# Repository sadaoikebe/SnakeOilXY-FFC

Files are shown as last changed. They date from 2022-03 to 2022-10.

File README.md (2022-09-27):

# FFC mod for SnakeOil-XY 3-D printer

This is a toolhead PCB suite for SnakeOil-XY 3-D printer.
* It's a combo of a toolhead PCB and a dedicated MCU. MCU is connected to the toolhead by a ribbon cable, which makes connection simpler and also makes toolhead lighter.
* It only needs USB wire and 24V power supply connected to the MCU board.
* It has an ADXL345 accelerometer on-board.
* It has an X endstop on board, which fits SnakeOilXY toolhead dimension.
* This system is compatible only with Klipper.

block diagram

## Appearance

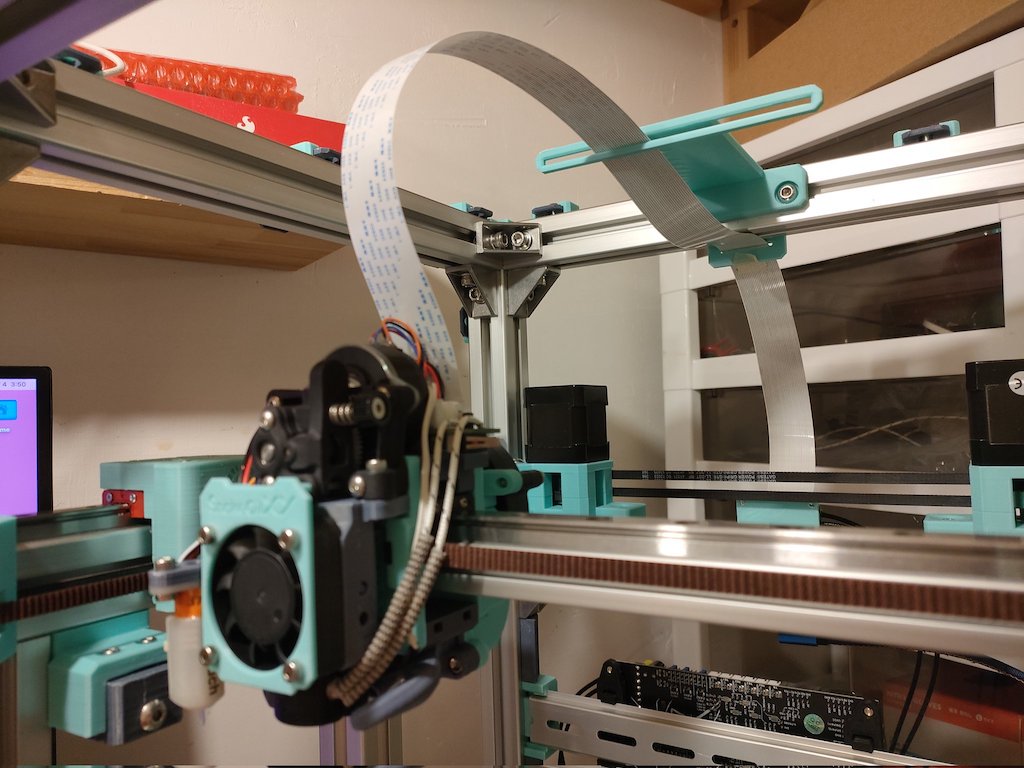
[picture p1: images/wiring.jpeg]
wiring


## Toolhead

This toolhead PCB can be attached onto adxl_mount to replace the ADXL345 PCB.

It's a toolhead PCB with an ADXL345 accelerometer on-board, and it has an X endstop which fits SnakeOil-XY toolhead dimension.

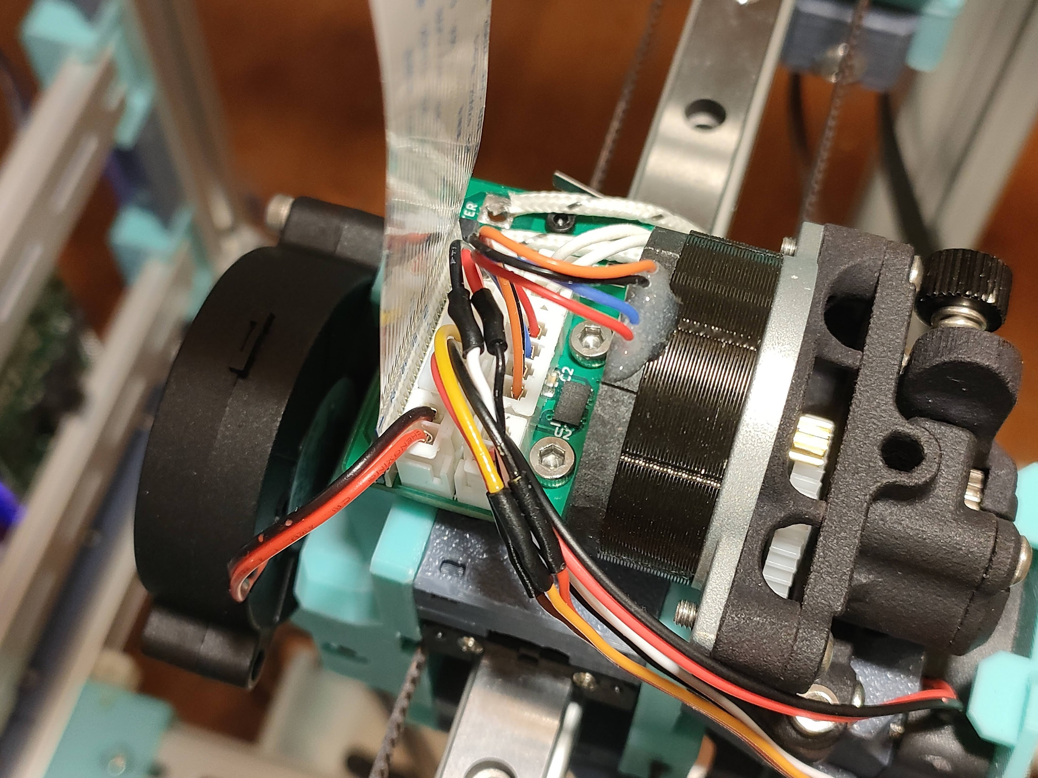
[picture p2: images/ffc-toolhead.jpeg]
Toolhead


### Toolhead board assembly

Tricky steps are:

* The two rows of the connectors are close, so two rows of connectors must be installed facing each other. Please be careful of the polarity of the hotend fan and the part cooling fan connector... (red arrow in the picture)
* Heater cables should be soldered. One of the heater terminals is close to the FFC connector, so unfortunately, screw terminal block (KF128 etc..) wouldn't fit. It's still able to disassemble without solder iron - loosening the bolt on the hotend will do the job. (yellow arrow in the picture)
* Bypass capacitor C2 is in the way of the stepper 4-pin connector. The bottom side of the stepper connector needs to be chamfered a little.
* It has Bltouch(servo) and Zmin(probe) connectors in order to use Z probes. Bltouch, inductive probe, or klicky probe can be used. See below diagram for connection.

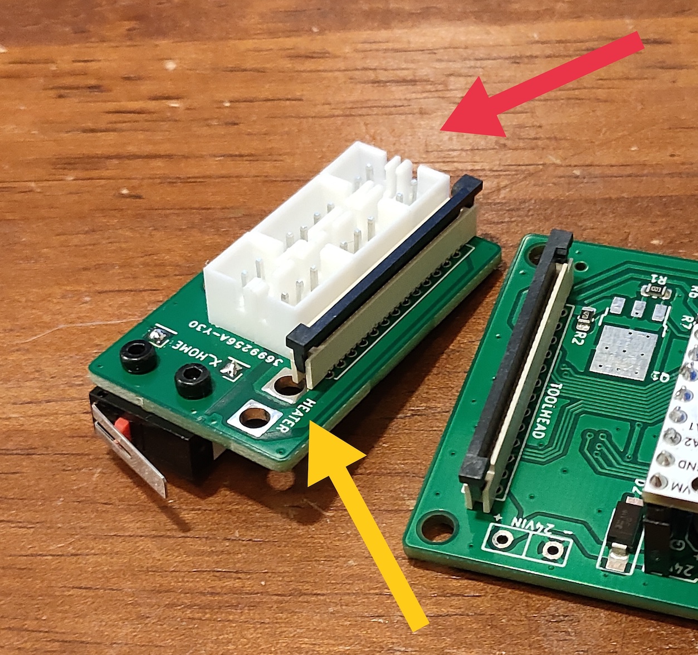
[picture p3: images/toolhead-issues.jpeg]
Toolhead


bltouch connection

induction probe connection
fan connection

### Toolhead board installation

It's designed to mount onto adxl_mount, however the X endstop switch is a bit thicker than the adxl_mount. Print and use spacer in the toolhead folder.

The back side of the stepper connector may touch the M3 bolt underneath the toolhead board. In order to avoid the unwanted contact, I recommend to cut the excess wire on the bottom and apply some capton tape to have better insulation.

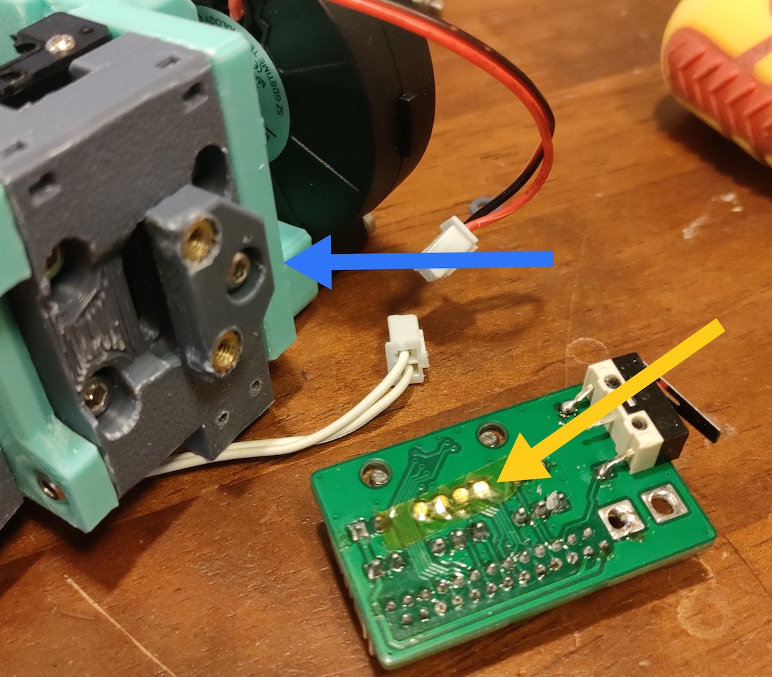
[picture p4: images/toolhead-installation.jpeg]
Toolhead


## MCU Board (revision 2)

For ease of connection, this board is dedicated to this FFC configuration. The MCU board just needs to be connected to the Raspberry Pi via USB and supplied with 24V power. A 1.0mm pitch 26-pin 20624 FFC cable is used.

It only supports UART-connected smart drivers (like TMC2209) for stepper motor driver. SPI or direct connections are not supported.

FFC connector can be soldered to either the front or back side of the board. Considering cooling and wiring, it's better to place it on the back side.

This board has schottky diode on it, so 24V probe can be connected to Zmin pin without frying the MCU.

Power => Blue LED

Heater and Fan MOSFETs => Yellow LED

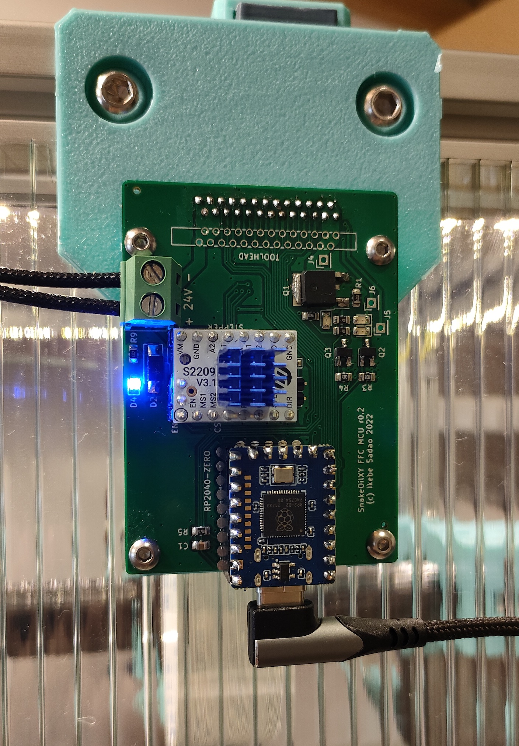
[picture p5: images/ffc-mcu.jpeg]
MCU board


### C1 capacity is too small
On the rev2 MCU board, the capacitance of C1 is 10uF, which does not stabilize the hotend temperature sensor reading enough. It would be better to add a larger capacitor in parallel or add a smooth_time setting in the [extruder] section.

## Klipper configuration

It assumes multi-mcu functionality of klipper firmware.

[sample printer.cfg](klipper/sample_printer.cfg)

## BOM

* RP2040-Zero
* 26-pin 350mm (180 model) / 450mm (250 model) 20624 FFC cable
* 2x 26-pin vertical thru-hole FFC receptacle
* 2x WSF3085 (MOSFET Heater)
* 2x PL4009 (MOSFET Fan)
* Stepper driver TMC2209 or other (UART connected "smart" drivers are must)
* 2-pin DC Terminal (KF128) for 24V power supply
* TVS diode (SMAJ28A) , schottky diode (1N5819) 40V
* 2x 8-pin socket (for stepper driver)
* Jumper pins
* Capacitors, resistors
* XH2.54 sockets (3x 2pin, 2x 3pin, 1x 4pin)

## TODO

### r0.1 --> r0.2

* The Drain and Source connections of the MOSFETs of the heater were reversed --> I changed the connections.
* TVS diode are reversed --> Thankfully JLCPCB engineer fixed it. Need to rotate next time.
* The clearance between the power supply/heater terminals and other parts are not enough --> Need increase the clearance.

### r0.2 --> r0.3

* Change MCU to genuine Pico as RP2040-Zero appears to be a bit unreliable
* add wiring and pattern for MAX31865 and PT100 thermistor
* add KF301 terminal for heater
* add AUX line
* add medusa toolhead support - allow for various X endstop placement

## Heater connection

The heater is assumed to be a 24V 50W, using 4 FFC cable contacts in parallel. Approx. 500mA current flows per contact.
Resistance of the heater wire is 266mΩ round trip including four screw terminals of 24V power supply and a 600mm FFC cable - which is measured by four-terminal-pair method.
When a 24V 50W heater is used, there is a loss of about 1W including circuits, cable and contacts. (225mΩ for 53cm of lead wire, 157mΩ for 14cm of lead wire, so the loss in the circuit and FFC is 133mΩ. 266mΩ round trip. This resistance value includes the resistance of four contacts on the fixture)

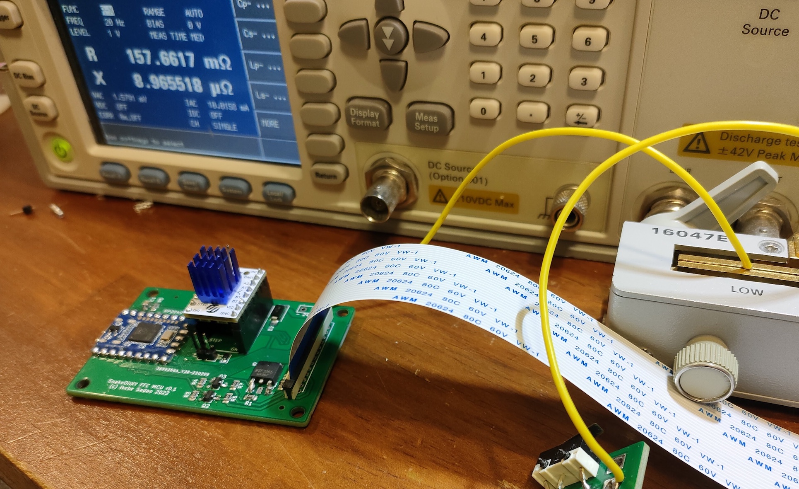
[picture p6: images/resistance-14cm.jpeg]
resistance-14cm

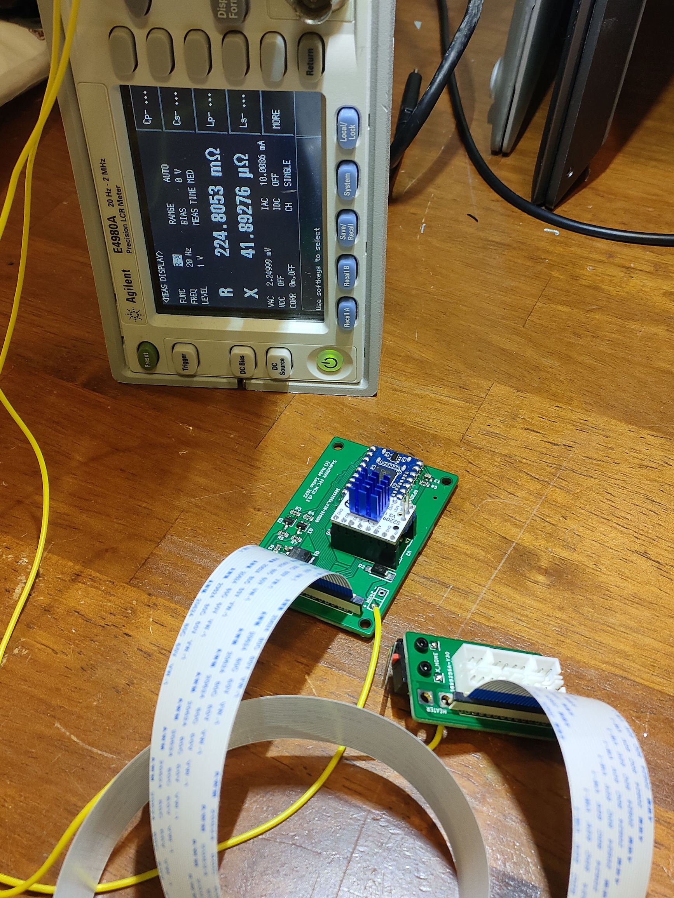
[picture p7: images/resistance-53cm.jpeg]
resistance-53cm


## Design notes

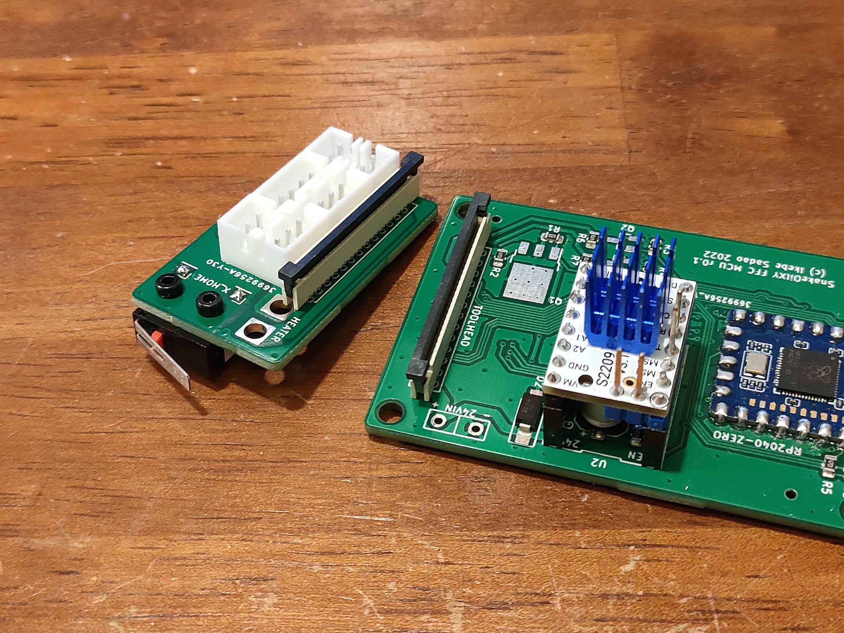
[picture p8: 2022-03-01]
images/boards.jpeg

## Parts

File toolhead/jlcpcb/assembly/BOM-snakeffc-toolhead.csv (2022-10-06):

Comment | Designator | Footprint | LCSC
0.1u | C2 | C_0603_1608Metric | C14663
ADXL345 | U2 | LGA-14_3x5mm_P0.8mm_LayoutBorder1x6y | C9667
SERVO | J11 | PinHeader_1x03_P2.54mm_Vertical
Conn_01x30 | J4 | ffc-30pin
ZMIN | J10 | PinHeader_1x03_P2.54mm_Vertical
HOTEND_FAN | J8 | PinHeader_1x02_P2.54mm_Vertical
HEATER | J5 | KF301-5.0
PARTCOOLER_FAN | J9 | PinHeader_1x02_P2.54mm_Vertical
E_STEPPER | J12 | PinHeader_1x04_P2.54mm_Vertical
X_HOME | J13 | limit_switch
AUX1 | J16 | PinHeader_1x01_P2.54mm_Vertical
PT100_NTC | J1 | PinHeader_1x04_P2.54mm_Vertical

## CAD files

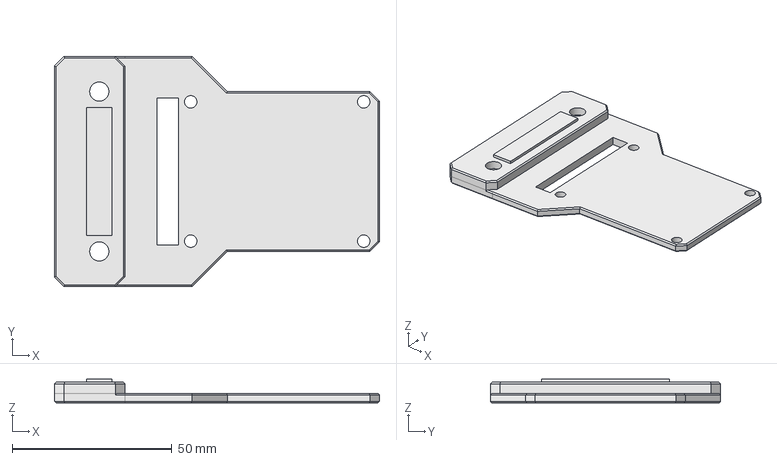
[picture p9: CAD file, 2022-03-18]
mcu2/mounter/mounter2.FCStd
101.6 x 72.0 x 7.50 mm

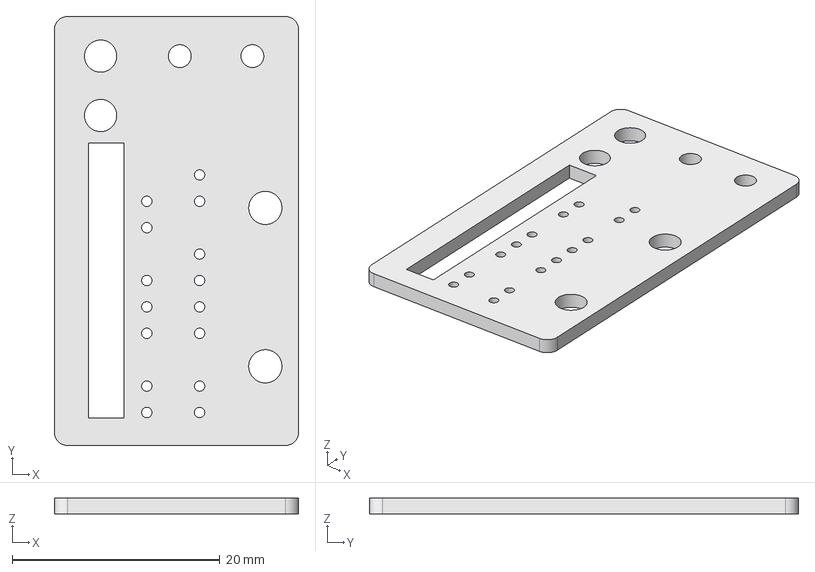
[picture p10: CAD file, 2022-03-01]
mockup/mockup.FCStd
23.5 x 41.3 x 1.50 mm

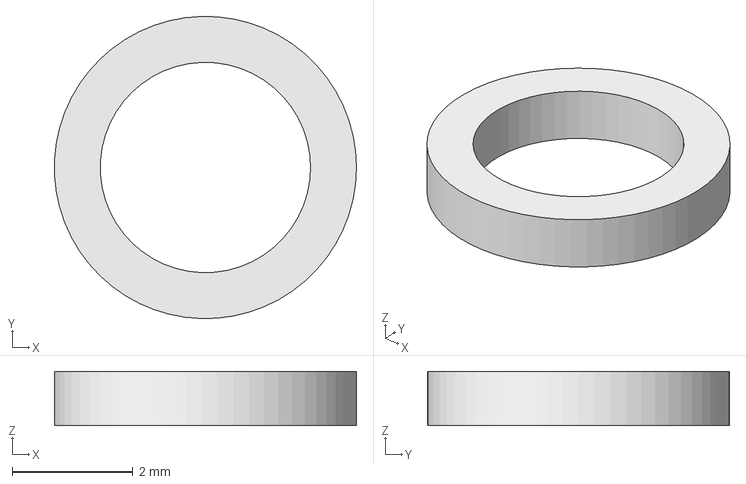
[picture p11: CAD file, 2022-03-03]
toolhead/adxl_mount_spacer.FCStd
5.00 x 5.00 x 0.9 mm

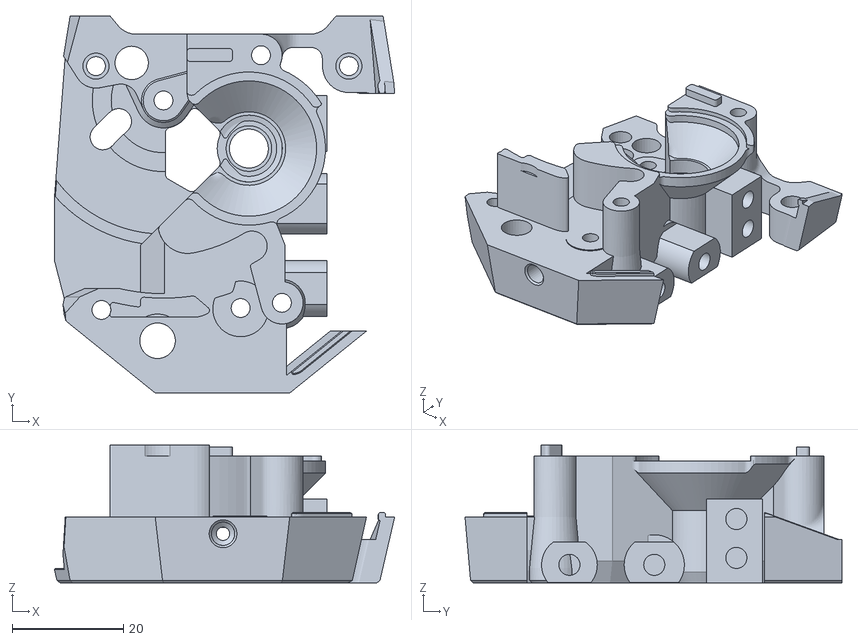
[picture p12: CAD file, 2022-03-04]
voron-clockwork2/sb-mod.stl
61.1 x 67.7 x 24.7

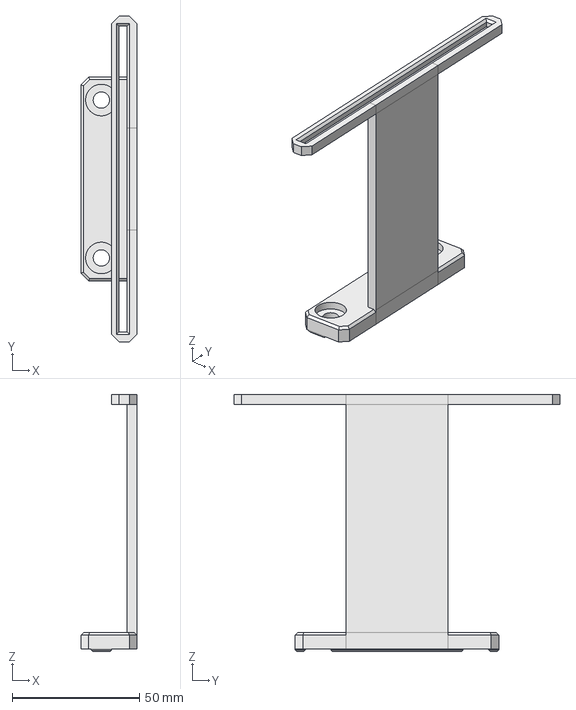
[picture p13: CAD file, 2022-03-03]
mcu2/mounter/cable-support2.FCStd
22.0 x 128.0 x 101.0 mm

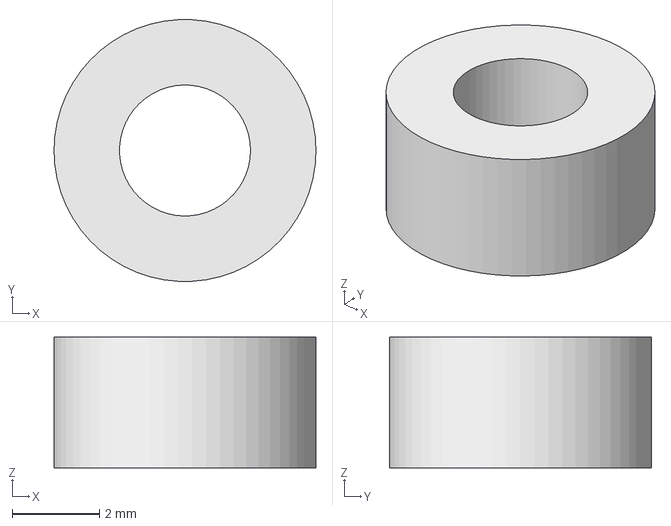
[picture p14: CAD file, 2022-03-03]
mcu2/mounter/mounter-spacer.FCStd
6.00 x 5.99 x 3.00 mm

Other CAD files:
mcu2/mounter/cable-support2.stl
mcu2/mounter/mounter-spacer.stl
mcu2/mounter/mounter2.stl
toolhead/adxl_mount_spacer.stl

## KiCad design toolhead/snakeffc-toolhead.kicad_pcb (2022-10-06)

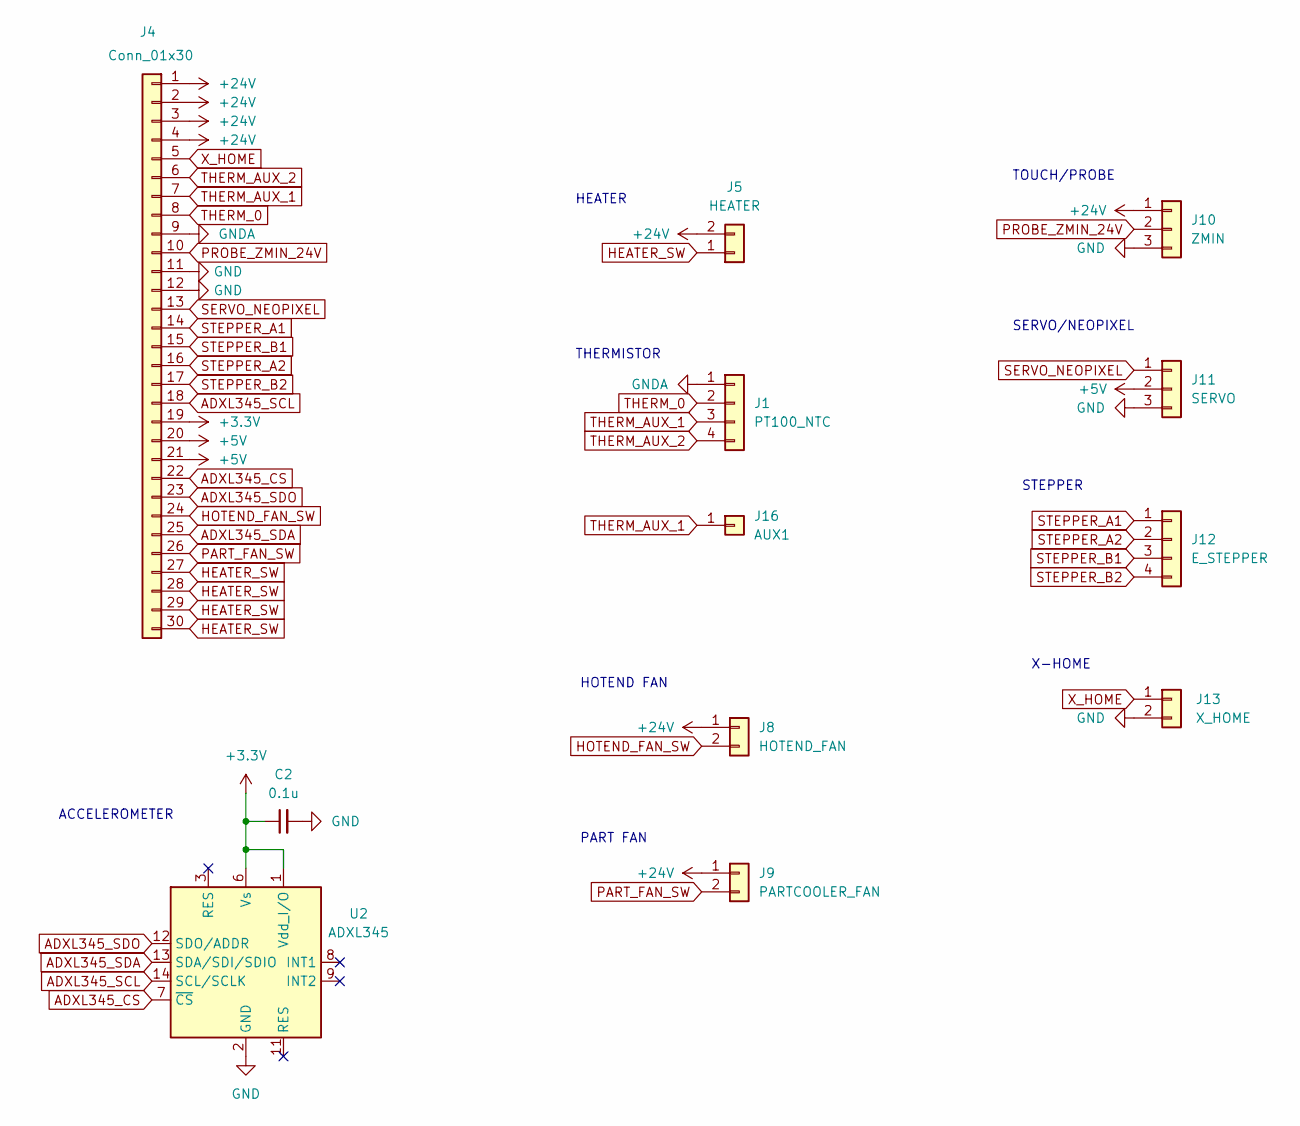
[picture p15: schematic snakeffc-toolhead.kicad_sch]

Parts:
C2: 0.1u; C_0603_1608Metric
J1: PT100_NTC; PinHeader_1x04_P2.54mm_Vertical
J4: Conn_01x30; ffc-30pin
J5: HEATER; KF301-5.0
J8: HOTEND_FAN; PinHeader_1x02_P2.54mm_Vertical
J9: PARTCOOLER_FAN; PinHeader_1x02_P2.54mm_Vertical
J10: ZMIN; PinHeader_1x03_P2.54mm_Vertical
J11: SERVO; PinHeader_1x03_P2.54mm_Vertical
J12: E_STEPPER; PinHeader_1x04_P2.54mm_Vertical
J13: X_HOME; limit_switch
J16: AUX1; PinHeader_1x01_P2.54mm_Vertical
U2: ADXL345; LGA-14_3x5mm_P0.8mm_LayoutBorder1x6y; LCSC C9667

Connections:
+3V3: C2.1, J4.19, U2.1 (Vdd_I/O), U2.6 (Vs)
+5V: J4.20, J4.21, J11.2
+24V: J4.1, J4.2, J4.3, J4.4, J5.2, J8.1, J9.1, J10.1
ADXL345_CS: J4.22, U2.7 (~CS)
ADXL345_SCL: J4.18, U2.14 (SCL/SCLK)
ADXL345_SDA: J4.25, U2.13 (SDA/SDI/SDIO)
ADXL345_SDO: J4.23, U2.12 (SDO/ADDR)
GND: C2.2, J4.11, J4.12, J10.3, J11.3, J13.2, U2.2 (GND), U2.4 (GND), U2.5 (GND)
GNDA: J1.1, J4.9
HEATER_SW: J4.27, J4.28, J4.29, J4.30, J5.1
HOTEND_FAN_SW: J4.24, J8.2
PART_FAN_SW: J4.26, J9.2
PROBE_ZMIN_24V: J4.10, J10.2
SERVO_NEOPIXEL: J4.13, J11.1
STEPPER_A1: J4.14, J12.1
STEPPER_A2: J4.16, J12.2
STEPPER_B1: J4.15, J12.3
STEPPER_B2: J4.17, J12.4
THERM_0: J1.2, J4.8
THERM_AUX_1: J1.3, J4.7, J16.1
THERM_AUX_2: J1.4, J4.6
X_HOME: J4.5, J13.1

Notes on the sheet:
PART FAN
HOTEND FAN
HEATER
STEPPER
X-HOME
ACCELEROMETER
THERMISTOR
SERVO/NEOPIXEL
TOUCH/PROBE

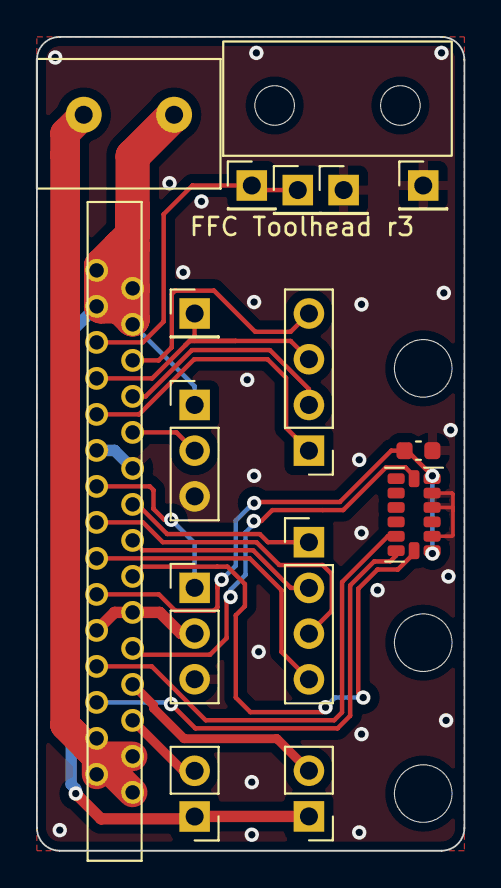
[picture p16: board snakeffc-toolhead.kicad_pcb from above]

Board: 2 copper layers, 23.7 x 45.2 mm, 12 parts (0 on the bottom side), 22 nets.

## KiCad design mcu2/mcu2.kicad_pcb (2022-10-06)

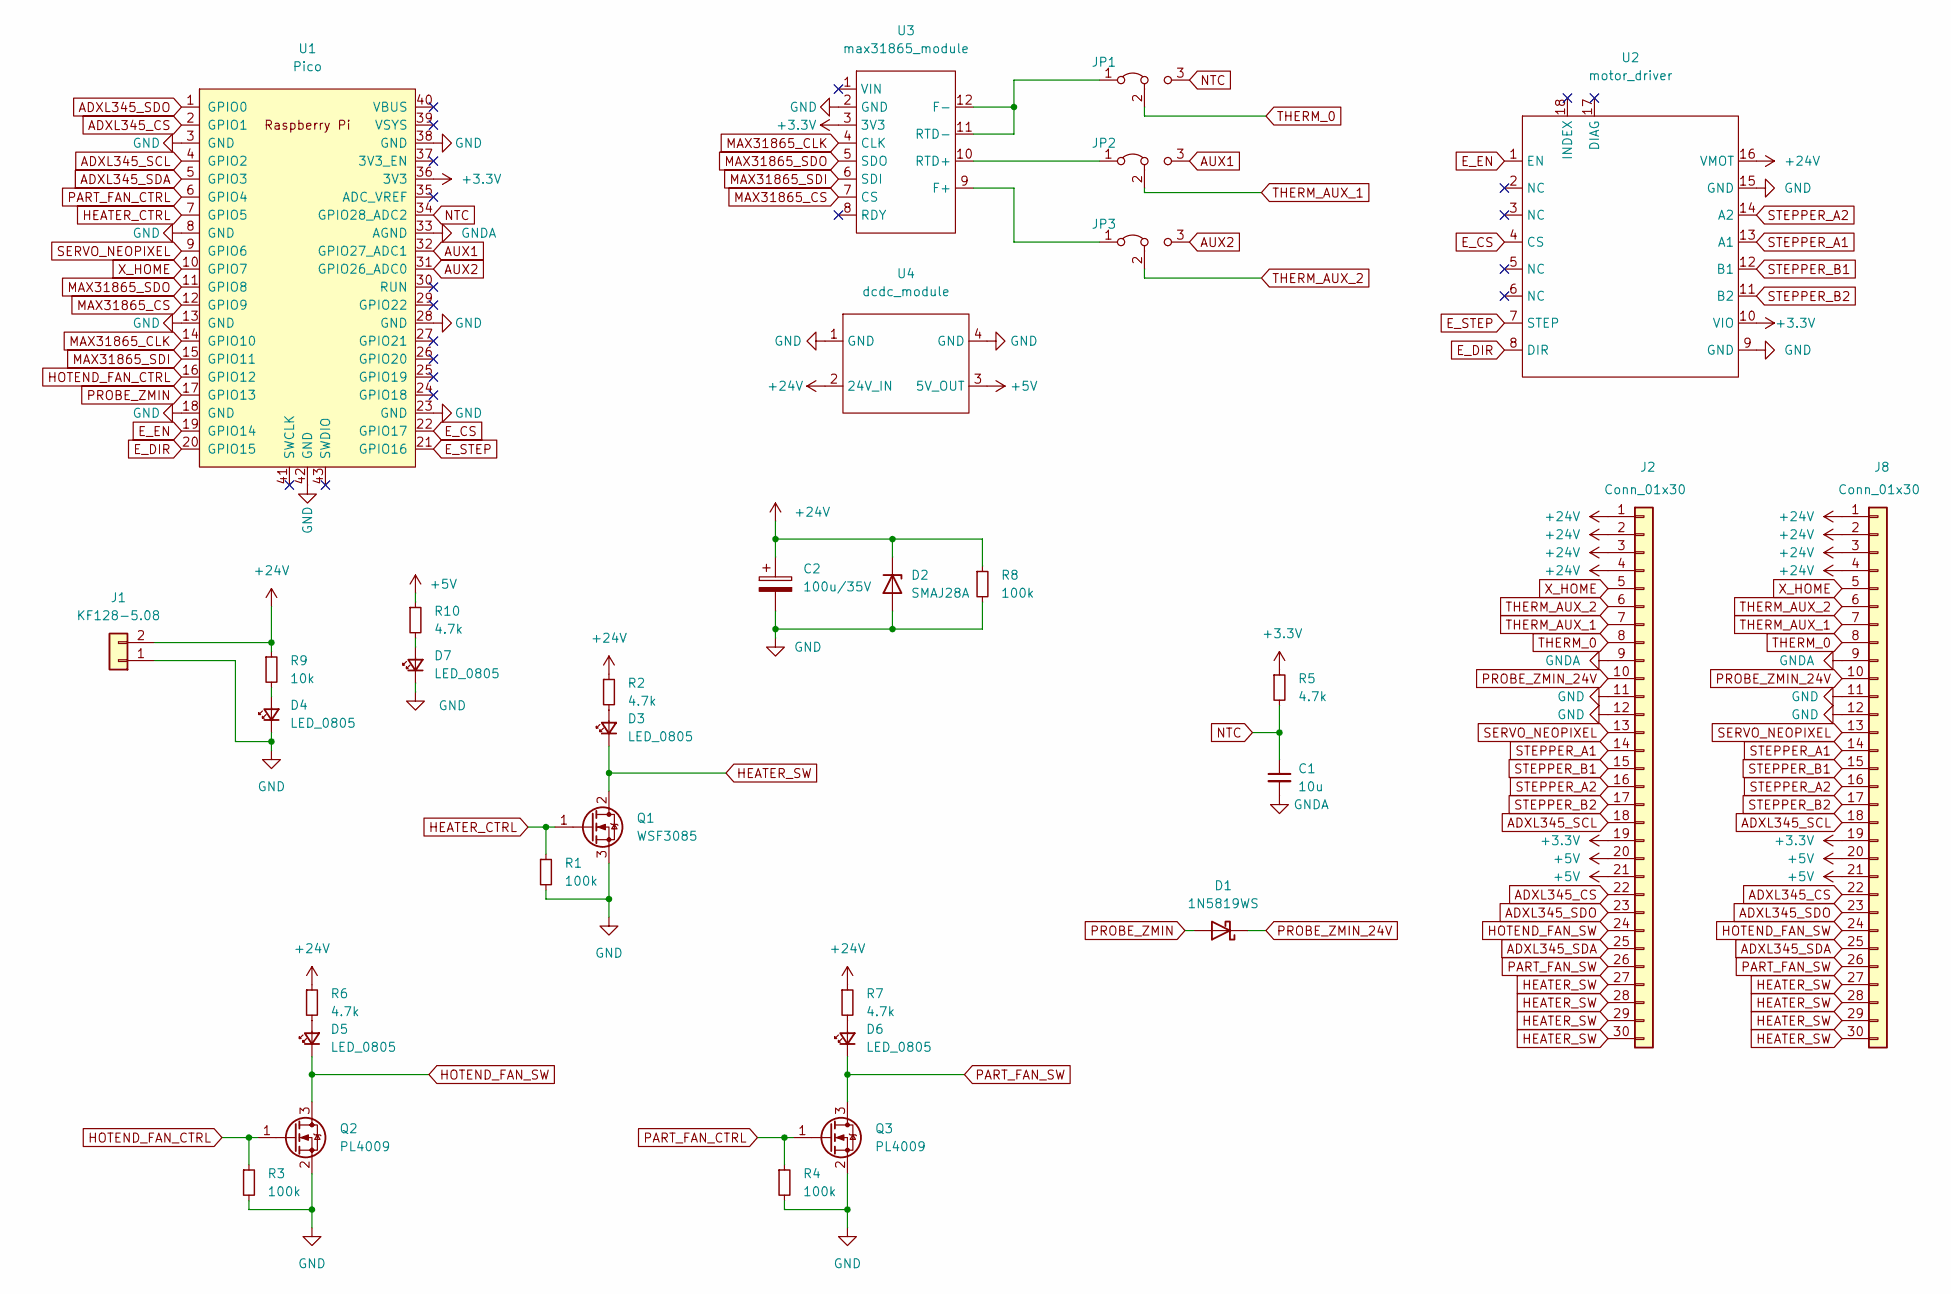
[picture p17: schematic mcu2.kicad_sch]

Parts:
C1: 10u; C_0805_2012Metric_Pad1.18x1.45mm_HandSolder
C2: 100u/35V; CP_Elec_6.3x7.7
D1: 1N5819WS; D_SOD-323_HandSoldering
D2: SMAJ28A; D_SMA_Handsoldering
D3, D4, D5, D6, D7: LED_0805; LED_0805_2012Metric_Pad1.15x1.40mm_HandSolder
J1: KF128-5.08
J2, J8: Conn_01x30; ffc-30pin
JP1, JP2, JP3: Jumper_3_Bridged12; SolderJumper-3_P1.3mm_Bridged12_RoundedPad1.0x1.5mm
Q1: WSF3085; TO-252-2
Q2, Q3: PL4009; SOT-23_Handsoldering
R1, R3, R4, R8: 100k; R_0805_2012Metric_Pad1.20x1.40mm_HandSolder
R2, R5, R6, R7, R10: 4.7k; R_0805_2012Metric_Pad1.20x1.40mm_HandSolder
R9: 10k; R_0805_2012Metric_Pad1.20x1.40mm_HandSolder
U1: Pico; RPi_Pico_SMD_TH
U2: motor_driver
U3: max31865_module; adafruit_max31865_module
U4: dcdc_module; dcdc_24v_5v_module

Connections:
+3V3: J2.19, J8.19, R5.1, U1.36 (3V3), U2.10 (VIO), U3.3 (3V3)
+5V: J2.20, J2.21, J8.20, J8.21, R10.1, U4.3 (5V_OUT)
+24V: C2.1, D2.1 (K), J1.2, J2.1, J2.2, J2.3, J2.4, J8.1, J8.2, J8.3, J8.4, R2.1, R6.1, R7.1, R8.1, R9.1, U2.16 (VMOT), U4.2 (24V_IN)
ADXL345_CS: J2.22, J8.22, U1.2 (GPIO1)
ADXL345_SCL: J2.18, J8.18, U1.4 (GPIO2)
ADXL345_SDA: J2.25, J8.25, U1.5 (GPIO3)
ADXL345_SDO: J2.23, J8.23, U1.1 (GPIO0)
AUX1: JP2.3 (B), U1.32 (GPIO27_ADC1)
AUX2: JP3.3 (B), U1.31 (GPIO26_ADC0)
E_CS: U1.22 (GPIO17), U2.4 (CS)
E_DIR: U1.20 (GPIO15), U2.8 (DIR)
E_EN: U1.19 (GPIO14), U2.1 (EN)
E_STEP: U1.21 (GPIO16), U2.7 (STEP)
GND: C2.2, D2.2 (A), D4.1 (K), D7.1 (K), J1.1, J2.11, J2.12, J8.11, J8.12, Q1.3 (S), Q2.2 (S), Q3.2 (S), R1.2, R3.2, R4.2, R8.2, U1.3 (GND), U1.8 (GND), U1.13 (GND), U1.18 (GND), U1.23 (GND), U1.28 (GND), U1.38 (GND), U1.42 (GND), U2.9 (GND), U2.15 (GND), U3.2 (GND), U4.1 (GND), U4.4 (GND)
GNDA: C1.2, J2.9, J8.9, U1.33 (AGND)
HEATER_CTRL: Q1.1 (G), R1.1, U1.7 (GPIO5)
HEATER_SW: D3.1 (K), J2.27, J2.28, J2.29, J2.30, J8.27, J8.28, J8.29, J8.30, Q1.2 (D)
HOTEND_FAN_CTRL: Q2.1 (G), R3.1, U1.16 (GPIO12)
HOTEND_FAN_SW: D5.1 (K), J2.24, J8.24, Q2.3 (D)
MAX31865_CLK: U1.14 (GPIO10), U3.4 (CLK)
MAX31865_CS: U1.12 (GPIO9), U3.7 (CS)
MAX31865_SDI: U1.15 (GPIO11), U3.6 (SDI)
MAX31865_SDO: U1.11 (GPIO8), U3.5 (SDO)
NTC: C1.1, JP1.3 (B), R5.2, U1.34 (GPIO28_ADC2)
unnamed: D3.2 (A), R2.2
unnamed: D4.2 (A), R9.2
unnamed: D5.2 (A), R6.2
unnamed: D6.2 (A), R7.2
unnamed: D7.2 (A), R10.2
unnamed: JP1.1 (A), U3.11 (RTD-), U3.12 (F-)
unnamed: JP2.1 (A), U3.10 (RTD+)
unnamed: JP3.1 (A), U3.9 (F+)
PART_FAN_CTRL: Q3.1 (G), R4.1, U1.6 (GPIO4)
PART_FAN_SW: D6.1 (K), J2.26, J8.26, Q3.3 (D)
PROBE_ZMIN: D1.2 (A), U1.17 (GPIO13)
PROBE_ZMIN_24V: D1.1 (K), J2.10, J8.10
SERVO_NEOPIXEL: J2.13, J8.13, U1.9 (GPIO6)
STEPPER_A1: J2.14, J8.14, U2.13 (A1)
STEPPER_A2: J2.16, J8.16, U2.14 (A2)
STEPPER_B1: J2.15, J8.15, U2.12 (B1)
STEPPER_B2: J2.17, J8.17, U2.11 (B2)
THERM_0: J2.8, J8.8, JP1.2 (C)
THERM_AUX_1: J2.7, J8.7, JP2.2 (C)
THERM_AUX_2: J2.6, J8.6, JP3.2 (C)
X_HOME: J2.5, J8.5, U1.10 (GPIO7)

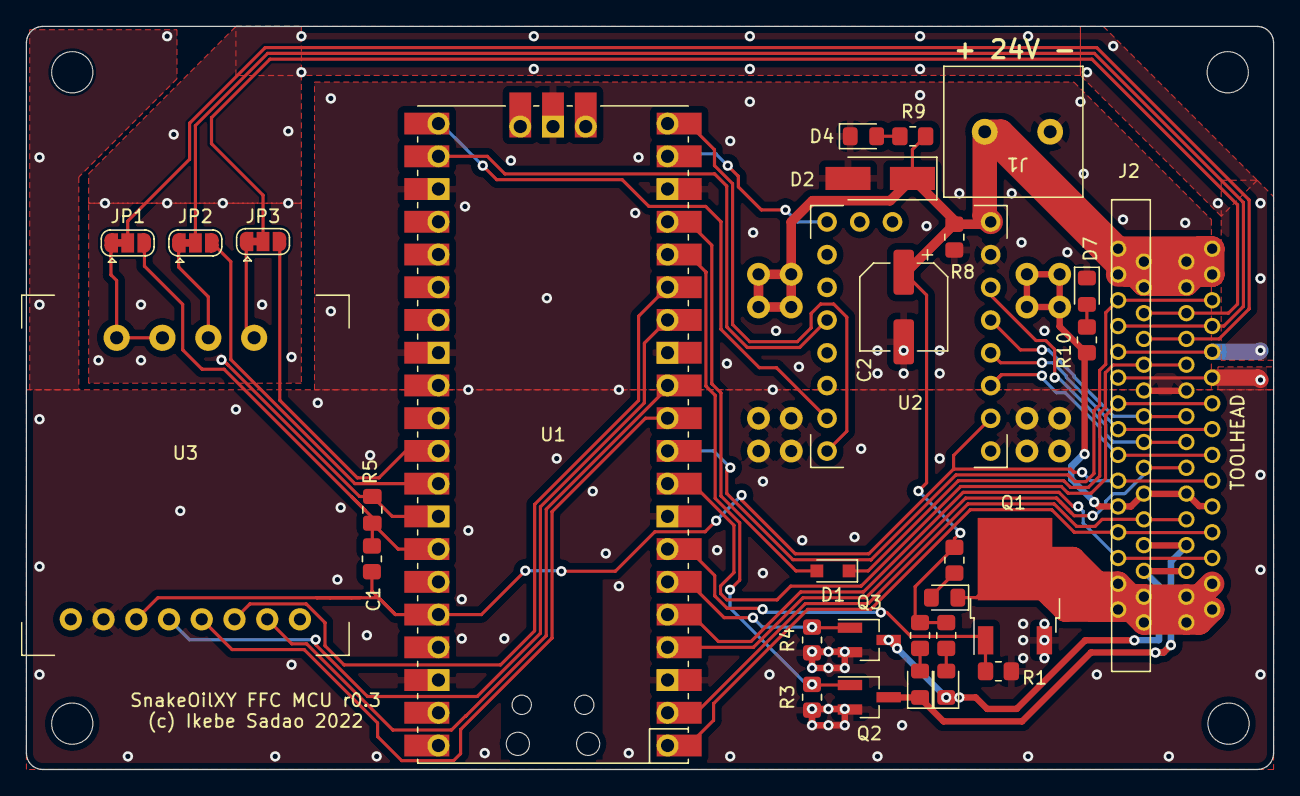
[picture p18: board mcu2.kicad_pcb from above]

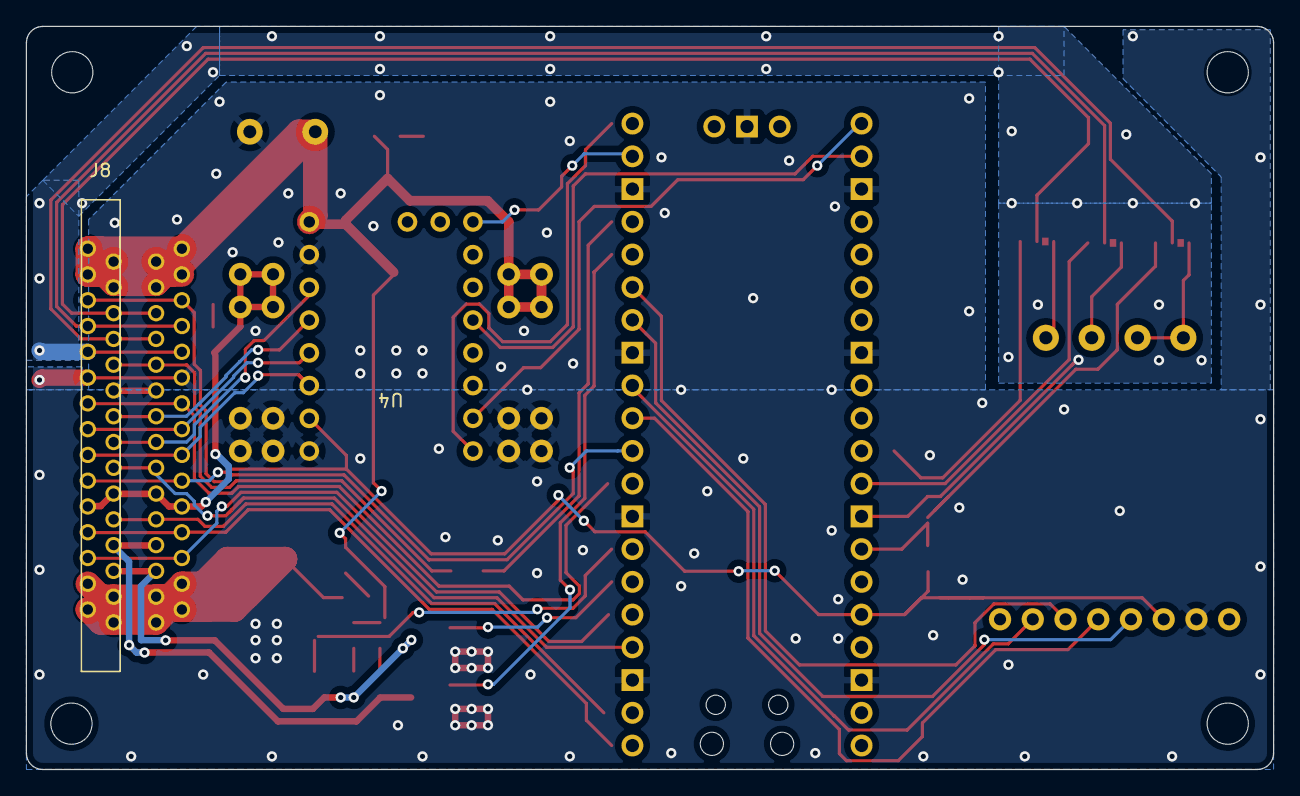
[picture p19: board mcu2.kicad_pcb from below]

Board: 2 copper layers, 96.8 x 57.7 mm, 32 parts (2 on the bottom side), 45 nets.

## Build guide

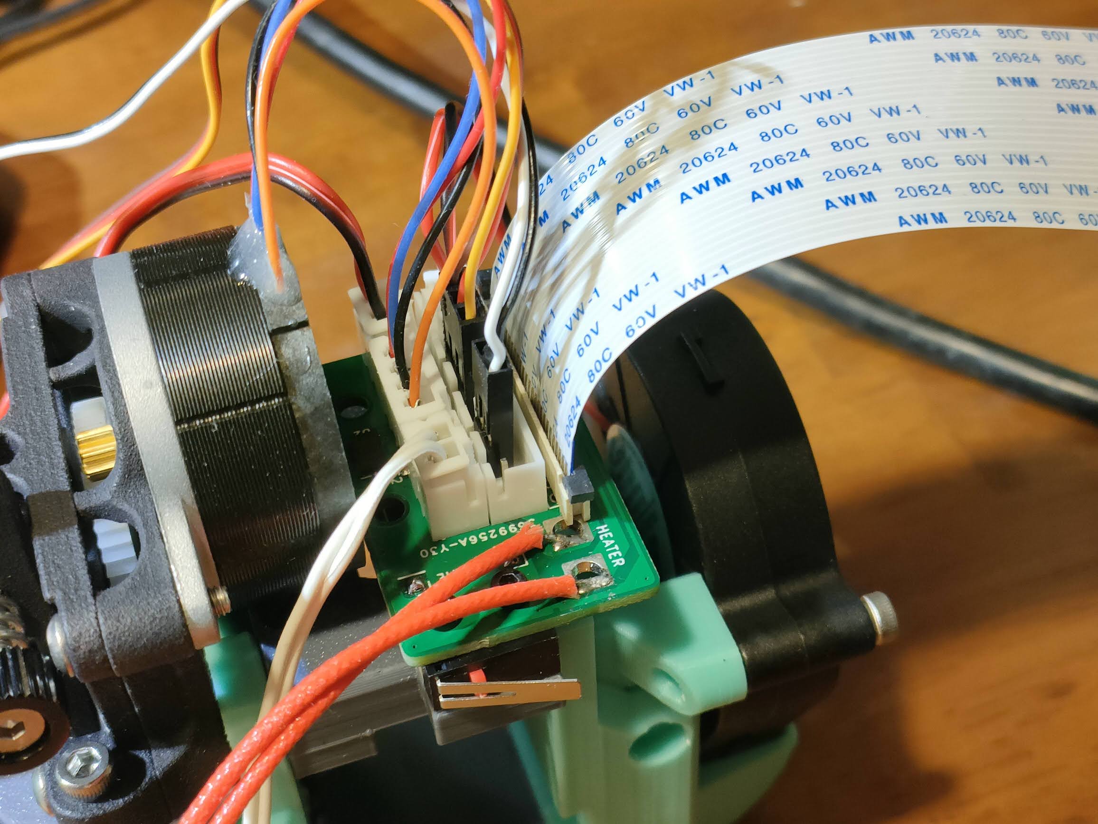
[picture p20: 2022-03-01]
images/toolhead-installed.jpeg

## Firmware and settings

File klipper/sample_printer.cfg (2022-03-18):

[include kiauh_macros.cfg]
[mcu]
serial: /dev/serial/by-id/usb-Klipper_stm32f446xx_160021001850563046363120-if00

[mcu toolhead]
serial: /dev/serial/by-id/usb-Klipper_rp2040_E66138935F119829-if00

[printer]
kinematics: corexy
max_velocity: 300  
max_accel: 10000
max_z_velocity: 15
max_z_accel: 350
square_corner_velocity: 5.0

[stepper_x]
step_pin: PE11
dir_pin: !PE10
enable_pin: !PE9
rotation_distance: 40
microsteps: 16
full_steps_per_rotation:400
endstop_pin: ^toolhead:gpio8
position_min: 0

position_endstop: 180
position_max: 180

homing_speed: 100
homing_retract_dist: 5
homing_positive_dir: true

[tmc2209 stepper_x]
uart_pin: PE7
interpolate: True
run_current: 0.7
hold_current: 0.4
sense_resistor: 0.110
stealthchop_threshold: 0

[stepper_y]
step_pin: PD8
dir_pin: !PB12
enable_pin: !PD9
rotation_distance: 40
microsteps: 16
full_steps_per_rotation:400
endstop_pin: ^PB13
position_min: 0

position_endstop: 180
position_max: 180

homing_speed: 100
homing_retract_dist: 5
homing_positive_dir: true

[tmc2209 stepper_y]
uart_pin: PE15
interpolate: True
run_current: 0.7
hold_current: 0.4
sense_resistor: 0.110
stealthchop_threshold: 0

[stepper_z]
step_pin: PD14
dir_pin: !PD13
enable_pin: !PD15
rotation_distance: 40
gear_ratio: 80:16
microsteps: 16
#endstop_pin: ^PA0
#position_endstop: 0
endstop_pin: probe:z_virtual_endstop
position_max: 180

position_min: -5
homing_speed: 8
second_homing_speed: 3
homing_retract_dist: 3

[safe_z_home]
home_xy_position: 90, 90
speed: 100
z_hop: 10
z_hop_speed: 5

[tmc2209 stepper_z]
uart_pin: PD10
uart_address: 0
interpolate: True
run_current: 0.7
hold_current: 0.4
sense_resistor: 0.110
stealthchop_threshold: 0

[adxl345]
cs_pin: toolhead:gpio1
spi_bus: spi0a

[resonance_tester]
accel_chip: adxl345
probe_points: 90, 90, 20

[bltouch]
sensor_pin: ^toolhead:gpio9
control_pin: toolhead:gpio7
z_offset: 0

[pause_resume]

[display_status]

[virtual_sdcard]
path: ~/gcode_files

##	In E0-MOT Position
[extruder]
step_pin: toolhead:gpio12
dir_pin: toolhead:gpio11
enable_pin: !toolhead:gpio10

rotation_distance: 22.6789511	#Bondtech 5mm Drive Gears
gear_ratio: 50:17				#BMG Gear Ratio
microsteps: 16
full_steps_per_rotation: 200	#200 for 1.8 degree, 400 for 0.9 degree
nozzle_diameter: 0.400
filament_diameter: 1.75
##      In E0 OUT Position
heater_pin: toolhead:gpio6
##	Validate the following thermistor type to make sure it is correct
sensor_type: ATC Semitec 104GT-2
sensor_pin: toolhead:gpio29
min_temp: 10
max_temp: 270
max_power: 1.0
min_extrude_temp: 170
control = pid
pid_kp = 26.213
pid_ki = 1.304
pid_kd = 131.721
##	Try to keep pressure_advance below 1.0
pressure_advance: 0.015
##	Default is 0.040, leave stock
pressure_advance_smooth_time: 0.040

##	In E0-MOT Position
##	Make sure to update below for your relevant driver (2208 or 2209)
[tmc2209 extruder]
uart_pin: toolhead:gpio13
interpolate: false
run_current: 0.5
hold_current: 0.2
sense_resistor: 0.110
stealthchop_threshold: 0

[heater_fan hotend_fan]
##  Hotend Fan - XYE board, HE1 Connector
pin: toolhead:gpio4
max_power: 1.0
kick_start_time: 0.5
heater: extruder
heater_temp: 50.0

[fan]
##  Print Cooling Fan - XYE board, Fan Pin
pin: toolhead:gpio5
kick_start_time: 0.5
off_below: 0.10



######################################################################
# "RepRapDiscount 128x64 Full Graphic Smart Controller" type displays
######################################################################

[display]
lcd_type: st7920
cs_pin: EXP1_4
sclk_pin: EXP1_5
sid_pin: EXP1_3
encoder_pins: ^EXP2_3, ^EXP2_5
click_pin: ^!EXP1_2
#kill_pin: ^!EXP2_8

[output_pin beeper]
pin: EXP1_1


########################################
# EXP1 / EXP2 (display) pins
########################################

[board_pins]
aliases:
    # EXP2 header
    EXP1_10=<5V>, EXP1_9=<GND>,
    EXP1_8=PD1,   EXP1_7=PD0,
    EXP1_6=PC12,  EXP1_5=PC10,     # Slot in the socket on the other side
    EXP1_4=PD2,   EXP1_3=PC11,
    EXP1_2=PA8,   EXP1_1=PC9,

    # EXP1 header
    EXP2_10=<5V>, EXP2_9=<GND>,
    EXP2_8=<RST>, EXP2_7=PB10,
    EXP2_6=PA7,   EXP2_5=PC7,       # Slot in the socket on the other side
    EXP2_4=PA4,   EXP2_3=PC6,
    EXP2_2=PA5,   EXP2_1=PA6

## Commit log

2022-02-07 gnd plane increased
    [BOM-snakeffc-toolhead.csv, snakeffc-toolhead.kicad_pcb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]
2022-02-07 sample config
2022-02-08 added stepper controller on the mcu
    [mcu2.kicad_sch]
2022-02-08 adjust hole position
2022-02-08 adjust holes and silkscreen
    [mcu2.kicad_sch]
2022-02-08 smd schottky and jumper, ordered JLCPCB
    [mcu2.kicad_sch]
2022-02-09 24V connector position adjusted - ordered again
2022-03-01 change footprint on heater mos
    [mcu2.kicad_sch, mockup.FCStd]
2022-03-03 add picture
    [adxl_mount_spacer.FCStd, adxl_mount_spacer.stl, cable-support.FCStd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]
2022-03-04 added sample printer.cfg, removed old mcu
    [sample_printer.cfg, snakeffc-mcu.kicad_sch]
2022-03-04 correct orientation for TVS diode
2022-03-04 add voron mod
    [sb-mod.stl]
2022-03-06 r2 jlcpcb
    [mcu2.kicad_sch]
2022-03-07 add a FFC connector on back side
    [mcu2.kicad_sch]
2022-03-18 mounter v2
    [mounter2.FCStd, mounter2.stl, sample_printer.cfg]
2022-03-18 make room for panels
    [mounter2.FCStd]
2022-03-22 add toolhead installation
    [cable-support.FCStd, cable-support.stl, mounter.FCStd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]
2022-03-25 sensor reading
2022-09-27 mcu schematic r3
    [mcu2.kicad_sch]
2022-09-27 toolhead r3 schematic
    [snakeffc-toolhead.kicad_sch]
2022-09-27 add footprints
    [mcu2.kicad_sch, snakeffc-toolhead.kicad_sch]
2022-09-27 remove unnecessary footprints
2022-09-28 mcu2 wiring
    [mcu2.kicad_sch]
2022-09-28 mcu2 gerber
    [mcu2.kicad_pcb, mcu2.kicad_sch]
2022-09-28 change hole size
    [mcu2.kicad_pcb]
2022-09-28 toolhead artwork
    [snakeffc-toolhead.kicad_pcb, snakeffc-toolhead.kicad_sch]
2022-10-06 r3 jlcpcb
    [BOM-snakeffc-toolhead.csv, mcu2.kicad_pcb, snakeffc-toolhead.kicad_pcb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]
